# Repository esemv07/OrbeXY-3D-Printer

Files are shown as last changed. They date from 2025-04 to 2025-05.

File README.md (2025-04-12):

# OrbeXY 3D Printer  ⚙️🛠️

A fully DIY 3D printer that I designed

##  Overview

This is a small CoreXY 3D printer that I have designed from scratch including designing the Toolhead, Bed Assembly, Gantry and Belt System, as well as the Optical Endstops. See my journey of designing and building the printer [here](https://github.com/esemv07/OrbeXY-3D-Printer/blob/main/JOURNAL.md). This printer costs under $476.04AUD ($300USD). See my list of materials and prices [here](https://github.com/esemv07/OrbeXY-3D-Printer/blob/main/BOM.md).

## ✨ Key Features

- CoreXY Kinematics
- 100mm<sup>3</sup> Build Area
- Under 250mm<sup>3</sup> Full Size
- Runs Klipper
- Remote Printer
- Pico MMU Compatible
- NEMA 14 Stepper Motors used for the X and Y Axes
- NEMA 17 Stepper Motor with Lead Screw used for the Z Axis
- Optical Endstops for Homing

## 🏆 Goals

For this printer there were a few things that I wanted to achieve:
1. ***A Compact Overall Size:*** I wanted this printer to fit into small desk space so that people can have easy access to printing without having to have a big area dedicated to the printer. I wanted the build area to also be fairly small, at 100mm<sup>3</sup>, making the printer suitable for quick, and small prints. A lot of the choices I made while designing this printer centred around having a compact size while still preserving the full 100mm<sup>3</sup> build area.
2. ***Runs Klipper with Remote Printing:*** I wanted the printer to run Klipper to improve the overall easy and quality of the printer. On top of this I wanted to have remote printing, so that you can start prints from anywhere and come home to an already started, or even finished print. This meant I had to consider the hardware I was using and how I could configure these parts into the Klipper software. This includes the Optical Endstops, which I designed myself, which will be configured to the Klipper file.
3. ***Pico MMU Compatible:*** I also wanted this printer to be able to print multicoloured if desired. To achieve this I have made the printer compatible with the Pico MMU, meaning that multicoloured prints can be printed if desired. This also meant that in the Klipper configuration file, I had to configure the MMU to make sure that I could still use it via remote printing.
4. ***Separated Spool Holder:*** I decided that in this printer, I would have the spool holder separate from the main printer. This aligns with my goal for the size constraints meaning that if the user does not have enough desk space for the spool as well, the spool could be stowed underneath the desk even while printing. The spool holder is connected to the printer via bowden tubing that will run from the spool holder, into the extruder. The same will apply for if the Pico MMU is used. The spool holders can stay under the desk as well as the Pico MMU and the bowden tubing will run from the Pico MMU to the extruder.

## 📋 Checklist

### Design:
- [x] Toolhead
- [x] Bed Assembly
- [x] Z Axis System
- [x] X and Y Axis Belt System
- [x] Screen Holder
- [ ] Motherboard and Battery Mount
- [ ] Spool Holder
- [ ] Full CAD Model

Here is the [link](https://a360.co/3FXQvPA) to my live updating Full CAD Model!

### Firmware:
- [ ] Remote Printing
- [ ] Configured Optical Endstops
- [ ] Pico MMU Configured
- [ ] Full Klipper config File

### Build:
- [ ] Assemble Gantry
- [ ] X and Y Axis Belt System
- [ ] Z Axis Assembly
- [ ] Bed Assembly
- [ ] Screen and Electronics
- [ ] Full Build

### Tuning:
- [ ] To be added

## 📸 Photos

### Design:

Will add when it is finished

### Build:

Will add as I build it

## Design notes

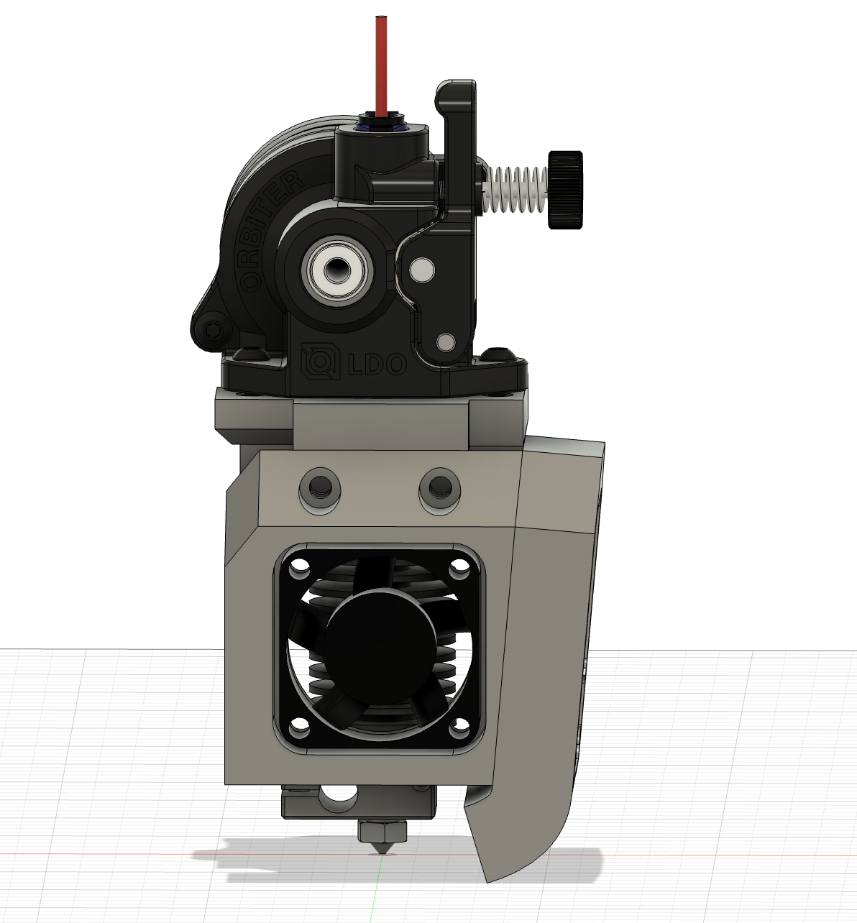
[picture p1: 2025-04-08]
progress-images/CAD-11:03:2025-1.png

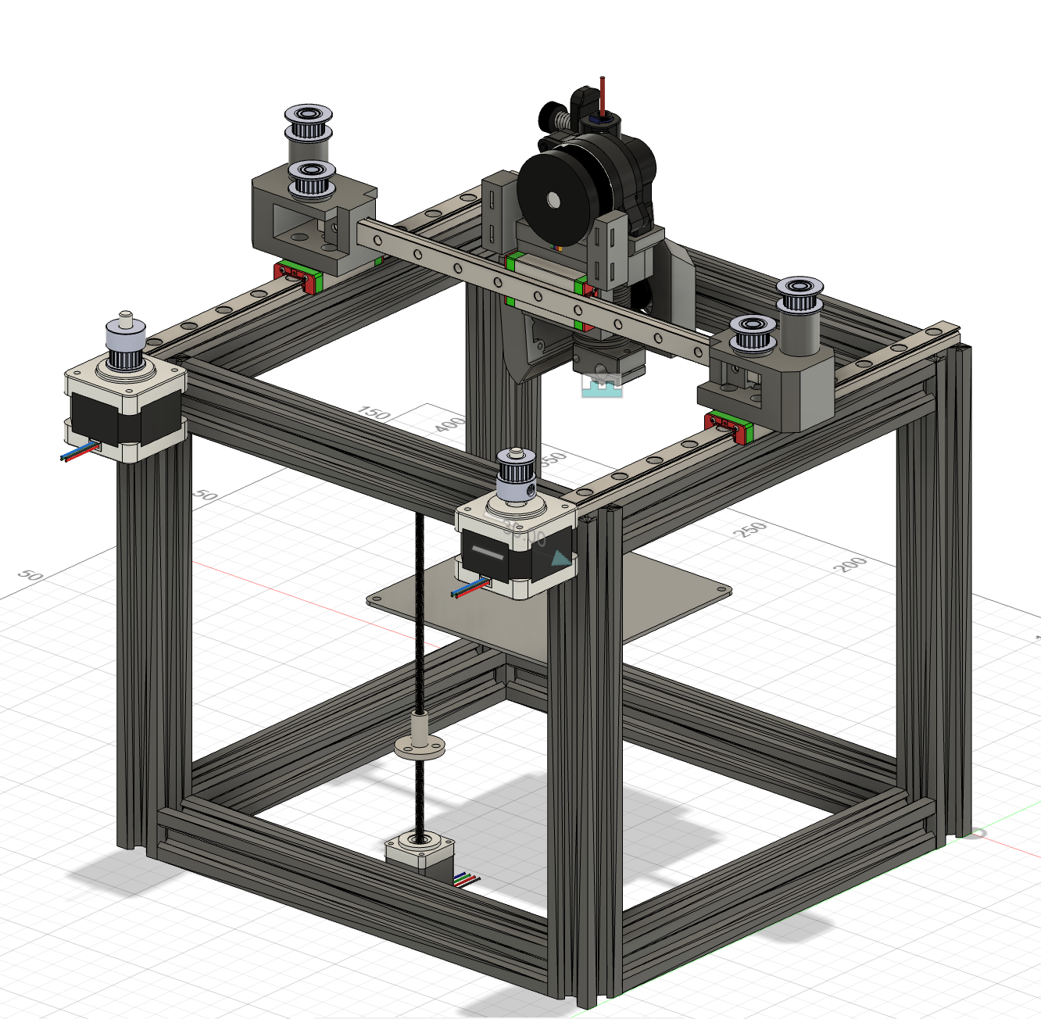
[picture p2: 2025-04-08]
progress-images/CAD-29:03:2025-2.png

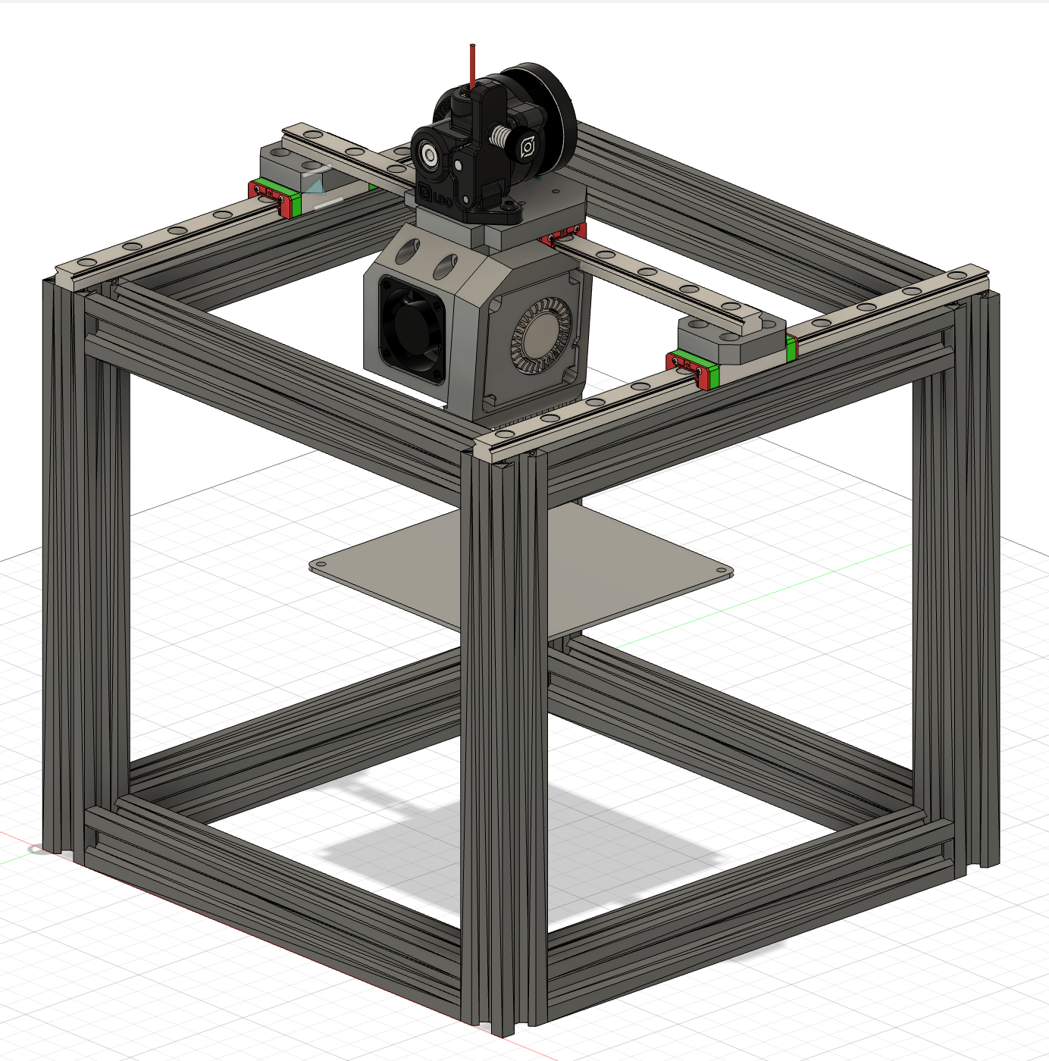
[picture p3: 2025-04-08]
progress-images/CAD-12:03:2025-1.png

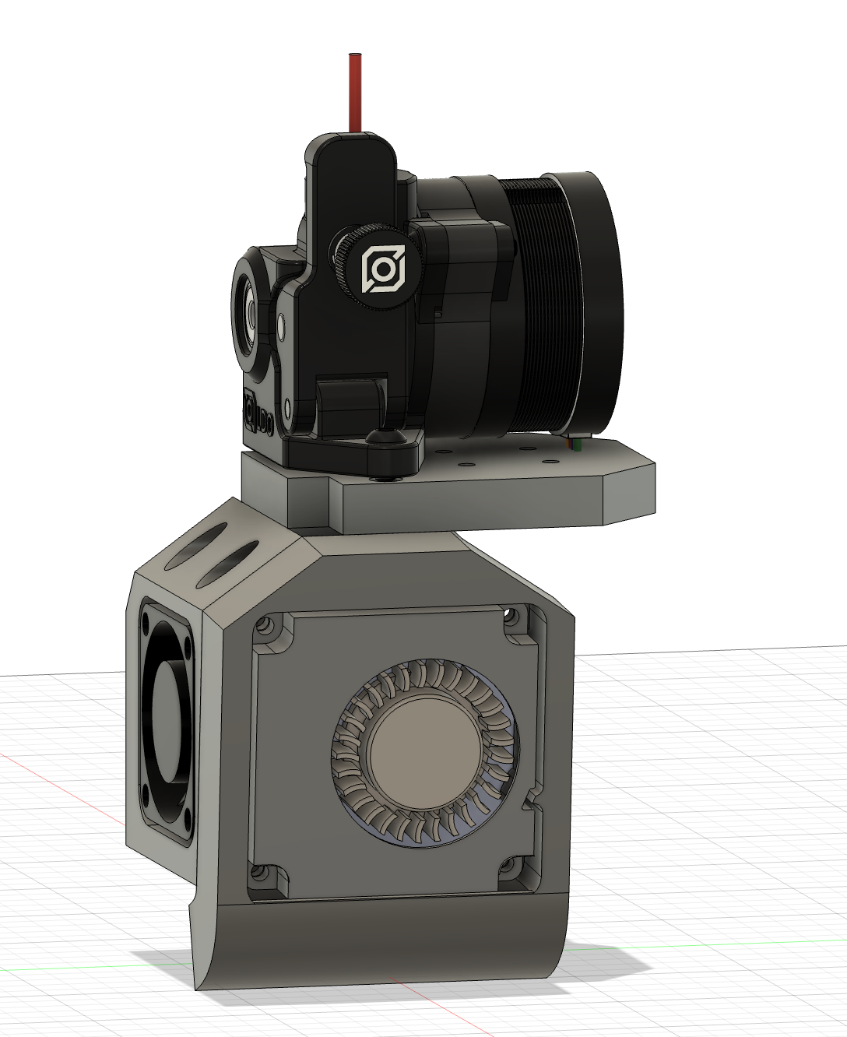
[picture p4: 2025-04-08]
progress-images/CAD-11:03:2025-2.png

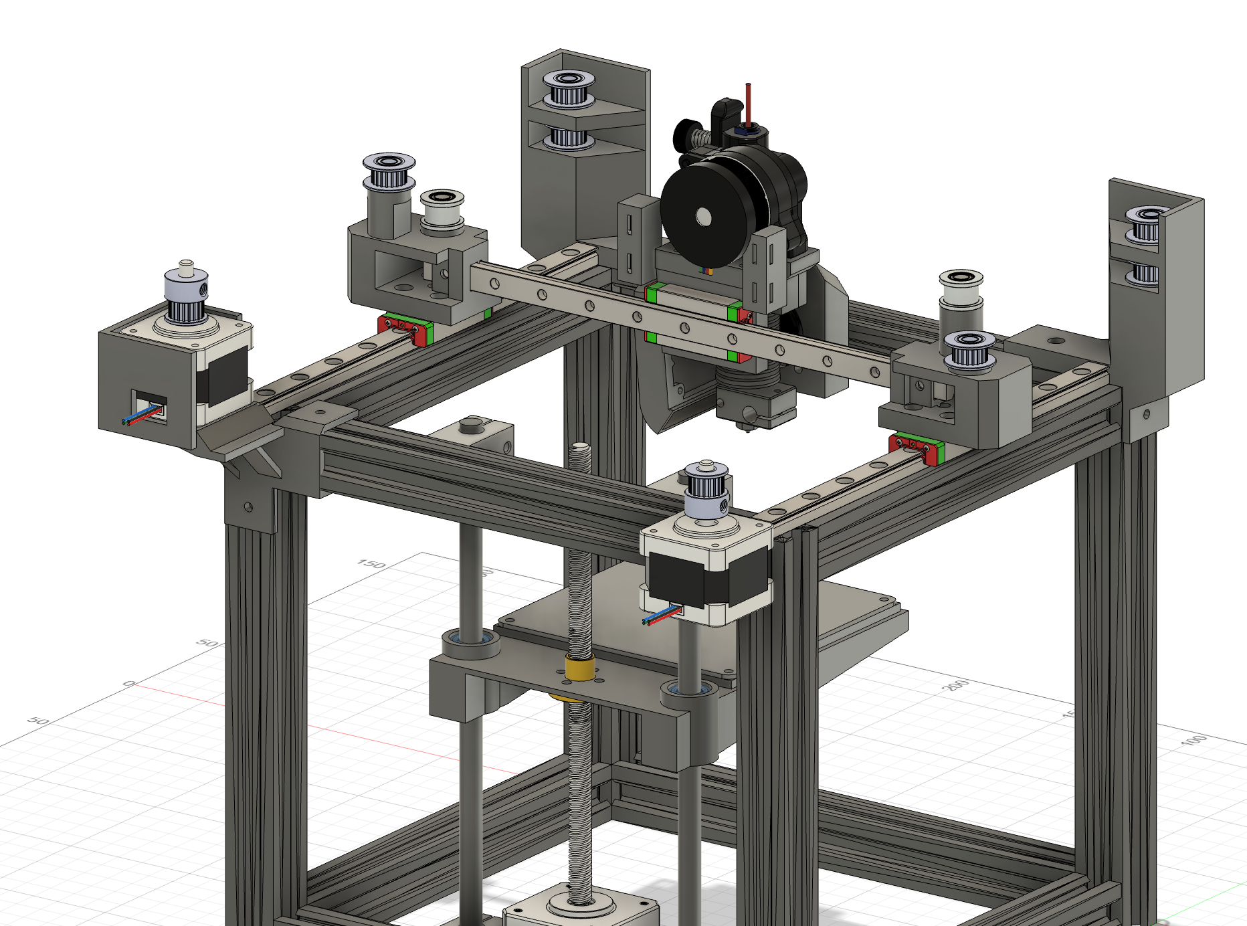
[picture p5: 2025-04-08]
progress-images/CAD-02:04:2025-2.png

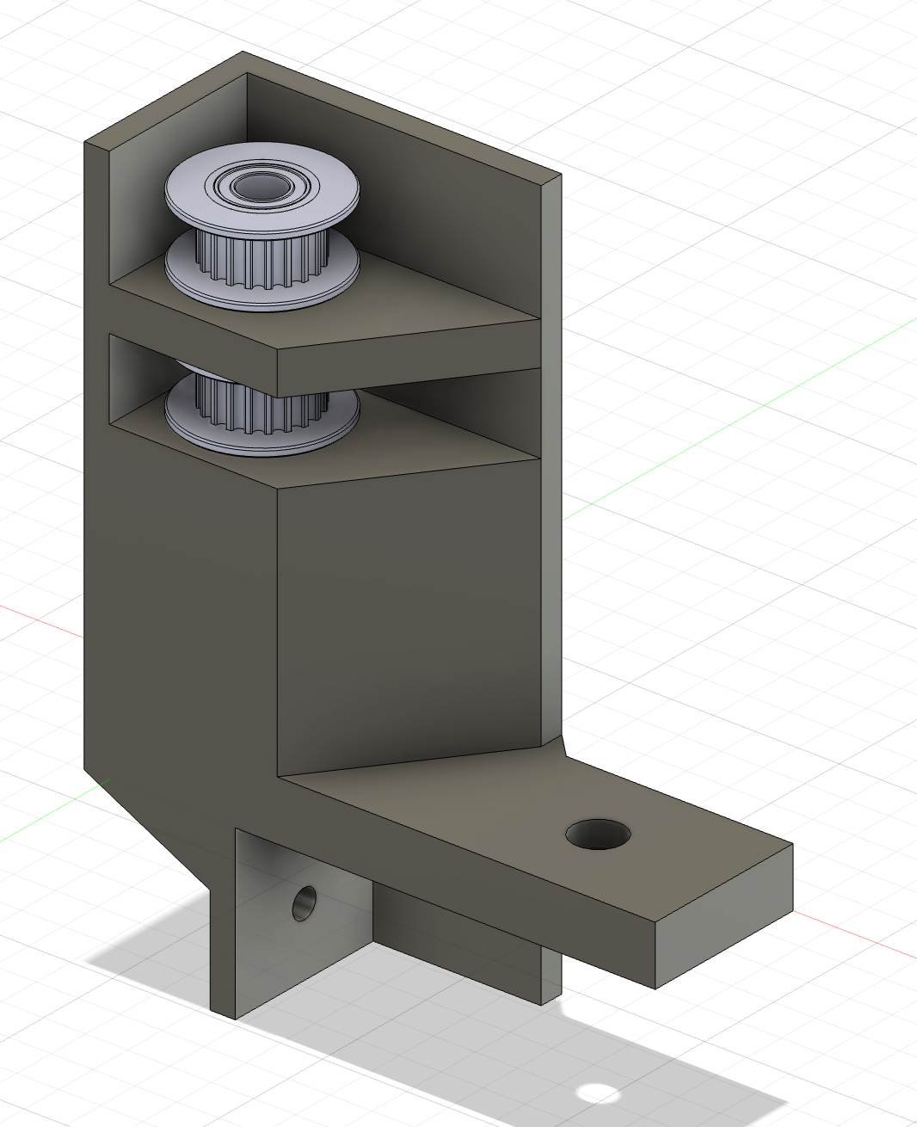
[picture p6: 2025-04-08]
progress-images/CAD-01:04:2025-1.png

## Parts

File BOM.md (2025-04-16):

# Bill Of Materials

Budget: $476.04AUD ($300USD)

> [!NOTE]  
> Prices may decrease as there is an upcoming sale.

> [!IMPORTANT]  
> Welcome deal will be used for the LCD Display Screen

| Category | Item | Price (AUD) | Quantity | Vendor | Link |
|---|---|---|---|---|---|
| Gantry ↓ | Aluminium Extrusions | $4.39 | 12 | AliExpress | [200mm 2020 T-slot Aluminum Profile](https://www.aliexpress.com/item/1005002845068178.html) |
| | MGN9H Linear Rails | $16.49 | 3 | AliExpress | [MGN9H Linear Rail](https://www.aliexpress.com/item/1005002937465647.html) |
| | GT2 Timing Pulley | $4.38 | 1 x 2pcs | AliExpress | [GT2 Timing Pulley](https://www.aliexpress.com/item/1005007708631215.html) |
| | GT2 20T Pulley | $2.46 | 6 | AliExpress | [GT2 20T 5mm Bore Pulley](https://www.aliexpress.com/item/1005005166638596.html) |
| | GT2 Smooth Idler Pulley | $2.46 | 2 | AliExpress | [GT2 Smooth 5mm Bore Pulley](https://www.aliexpress.com/item/1005005166638596.html) |
| | GT2 Timing Belt | $3.42 | 1 | AliExpress | [GT2 Closed Loop Timing Belt 6mm](https://www.aliexpress.com/item/32477498985.html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) |
| | NEMA 14 Stepper Motor | $8.35 | 2 | AliExpress | [NEMA 14 0.9 Degree 35MM Stepper Motor](https://www.aliexpress.com/item/1005008564455087.html) |
| Toolhead ↓ | Orbiter V2.0 | $36.59 | 1 | AliExpress | [Orbiter Extruder V2.0](https://www.aliexpress.com/item/1005006369780118.html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) |
| | E3D V6 Hotend | $7.71 | 1 | AliExpress | [E3D V6 Hotend 24V Short with PTFE](https://www.aliexpress.com/item/1005003651646732.html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) |
| | 3010 Axial Fan | $3.23 | 1 | AliExpress | [3010 Axial Fan 24V](https://www.aliexpress.com/item/1005003999728858.html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) |
| | 4010 Blower Fan | $3.68 | 1 | AliExpress | [4010 Blower Fan 24V](https://www.aliexpress.com/item/1005003999728858.html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) |
| | LDO Stepper Motor | $38.06 | 1 | AliExpress | [LDO-36STH20-1004AHG](https://www.aliexpress.com/item/1005005709255487.html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) |
| Bed Assembly ↓ | Mini Heated Bed | $17.44 | 1 | OpenBuilds | [Mini Heated Bed](https://us.openbuilds.com/mini-heated-bed/) |
| | Magnetic PEI Plate | $17.42 | 1 | AliExpress | [120x120mm Magnetic PEI Sheet](https://www.aliexpress.com/item/1005006868711474.html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) |
| | Silicone Foam Sheet | $1.53 | 1 | AliExpress | [100x100x3mm Red Silicone Foam Mat](https://www.aliexpress.com/item/1005008602779260.html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) |
| | NEMA 17 Motor w/ Lead Screw  | $26.79 | 1 | AliExpress | [NEMA17 Stepper Motor T8 Lead Screw Kit](https://www.aliexpress.com/item/1005004105159462.html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) |
| | Linear Rod | $4.13 | 2 | AliExpress | [200x8mm Stainless Steel Rod](https://www.aliexpress.com/item/1005008351656218.html) |
| | LM8UU Linear Bearing | $3.54 | 1 x 2pcs | AliExpress | [LM8UU Linear Bushing 8mm](https://www.aliexpress.com/item/1005008687738190.html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) |
| | SK8 Linear Rail Mount | $9.93 | 1 x 4pcs | AliExpress | [SK8 Linear Bearing Rail Shaft Support](https://www.aliexpress.com/item/4000909598267.html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) |
|  Electronics ↓ | SKR MINI E3 V3.0 Motherboard | $47.59 | 1 | AliExpress | [BIGTREETECH BTT SKR MINI E3 V3.0 Motherboard](https://www.aliexpress.com/item/1005008626893863.html) |
| | LCD Display Screen | $12.72 | 1 | AliExpress | [BIGTREETECH MINI 12864 V2.0 LCD Display Screen](https://www.aliexpress.com/item/1005006135086424.html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) |
| | Power Supply | $27.24 | 1 | eBay | [24V 350W Power Supply](https://www.ebay.com.au/itm/116529752336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) |
| | Plug and Switch Module | $3.61 | 1 | AliExpress | [Power Switch AC Power Outlet](https://www.aliexpress.com/item/32857063415.html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,scm-url:1007.40196.417130.0,pvid:38387bd7-0782-4954-80dd-48ccc1529973,tpp_buckets:668%232846%238110%231995&pdp_ext_f=%7B%22order%22%3A%22622%22%2C%22eval%22%3A%221%22%2C%22sceneId%22%3A%2230050%22%7D&pdp_npi=4%40dis%21AUD%213.80%211.68%21%21%212.24%210.99%21%402103146c17441867923614998e6107%2166407555495%21rec%21AU%21%21ABX&utparam-url=scene%3ApcDetailTopMoreOtherSeller%7Cquery_from%3A) |
| | Raspberry Pi Zero 2 W | N/A | 1 |(From Home) | N/A |

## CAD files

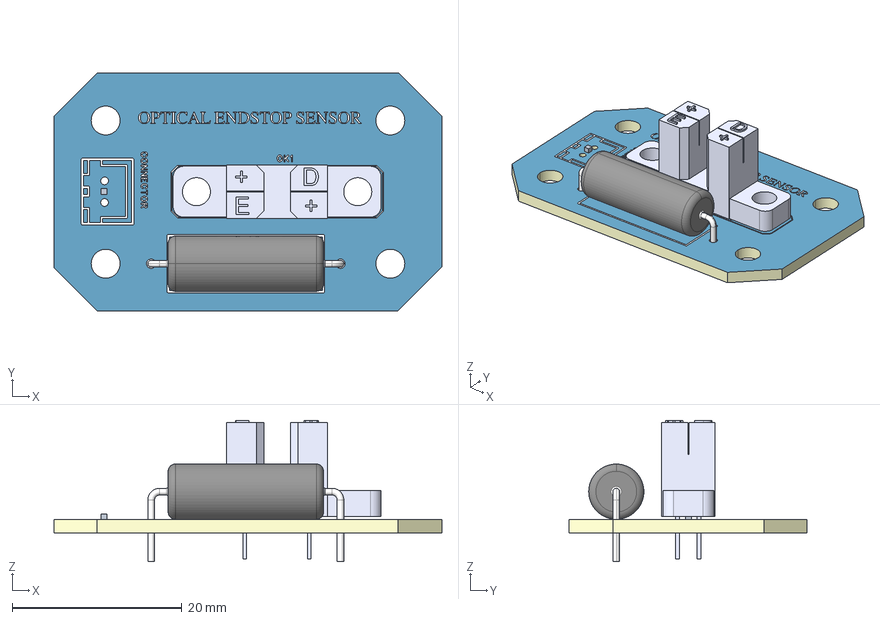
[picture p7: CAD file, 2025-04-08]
pcb/3D_1-PCB_PCB_Optical Endstops_2025-04-07.step
45.7 x 28.0 x 16.7 mm
Board~oxxd
TopCopper~oxxd
BottomCopper~oxxd
TopSilkscreen~oxxd
TopFpcStiffener~oxxd
BottomFpcStiffener~oxxd
TCST-2103~SENSORS-TH_TCST2103~oxxd
RES-TH_L18.3-W6.5-P22.30-D0.8~RES-TH_L18.3-W6.5-P22.30-D0.8~oxxd
JST_2-PIN_2.54MM~Connector_JST/JST - XH - Thru - 2Pin - 2.54mm~oxxd

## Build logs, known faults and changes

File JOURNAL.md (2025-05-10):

Made by: @esemv

Repository link: https://github.com/esemv07/OrbeXY-3D-Printer

Total hours so far: 64 hours

- [x] I have a 3D printer or will be getting one before March 21st

## What Makes My Printer Unique?
### Goals
- CoreXY Kinematics
- Under 280mm<sup>3</sup> total size
- 100mm<sup>3</sup> build volume
- Runs Klipper
- Pico MMU Compatible
- Remote Printing

### Achieved So Far
- [x] CoreXY Kinematics
- [x] Under 280mm<sup>3</sup> total size
- [x] 100mm<sup>3</sup> build volume
- [ ] Runs Klipper
- [ ] Pico MMU Compatible
- [ ] Remote Printing

## Day 1: March 8th 2025 
`Reseach` `PCB` `CAD`
- I reseached materials and what would be compatible with each other while staying in budget and my size constraints. I decided on an Extuder (Obbiter V2.0), and a Motherboard (BigTreeTech SKR Mini E3 V3.0). 

- I found a potential option for a printbed. It is quite difficult to find one that is in the correct size (100x100mm) as most come in 120x120 for the smallest size. I have decided that for the PEI Plate, I will buy a bigger size and cut it to the correct dimensions myself.

- I then designed a quick and simple PCB for the small Optical Endstop Sensors that I can use to keep the printhead in build area for all axes.

`Research: +3 hours` `PCB: +1 hour`

***+4 hours***

- I also researched different methods of multicolour printing and what would take up less space. Started designing a PCB for a Rotary Switcher Multi Material System, but then realised it would be to big for my printer size. I settled on using an MMU but I think I will design that last so I get the core mechanics good first.

CAD Mockup

- Started a rough CAD model in Fusion of the frame to visualise the dimensions. I may change the 2020 Aluminium Extrusions to 1010.

`Research: +1 hour` `CAD: +2 hours`

***+3 hours***

### Time Spent on This Day: 7 hours 
`Research: 4 hours` `PCB: 1 hour` `CAD: 2 hours`

<br><br>
## Day 2: March 9th 2025
`Research` `CAD`

CAD Frame Reshape

- I reshaped the frame so that there was more space on the inside and it will be less confusing for physical connection when I build it. It is now 200mm<sup>3</sup>, using 8 x _2020 160mm Aluminium Extrusions_ and 4 x _2020 200mm Aluminium Extrusions_.

- I then researched power supplies - how they work, how to know what voltage, current, and wattage to use. I also researched different methods for the Z-Axis on a CoreXY printer. I figured out that due to the very small scale of my printer I won't need to support all 4 corners of the build plate.

- I also reasearched hotends and how to connect them to my extruder which is direct drive. I am going to design a 3D printable mount so I can connect my direct drive extruder (Orbiter V2.0) with my hotend (Short E3D V6 Hotend with PTFE).

`Research: +3 hours` `CAD: +30 mins`

***+3 hours 30 mins***

### Time Spent on This Day: 3 hours 30 mins

`Research: 3 hours` `CAD: 30 mins`

<br><br>
## Day 3: March 10th 2025
`Research` `CAD`

- I researched toolhead designs and what fans I could use for mine and how I could mount the extruder to the hotend.

`Research: +1 hour`

***+1 hour***

CAD Toolhead

- I designed the toolhead with different parts that would mount together using screws and heatset inserts.

- There are 3 different parts: the part that mounts to the front of the hotend, the part that connects the axial fan to that part, and the part that mounts to the back of the hotend connecting the other fan and the extruder.

CAD Toolhead in Assembly

- Here is what it looks like in the full assembly so far.

`CAD: +3 hours`

***+3 hours***

CAD Toolhead Angled

- I also changed the angle of the side fan to blow the air more towards the nozzle and to optimise space on the toolhead.

`CAD: +1 hour`

***+1 hour***

### Time Spent on This Day: 5 hours

`Research: 1 hour` `CAD: 4 hours`

<br><br>
## Day 4: March 11th 2025

`Research` `CAD`

- I did more research on toolheads and realised that I need to add a channel for the air to flow towards the nozzle. I researched different methods of this for my design.

CAD Toolhead Airflow 1 CAD Toolhead Airflow 2

- I then applied this to my CAD model trying not to impede on the parts that I already had. This proved much harder than I expected and I had many iterations of it before I finally achieved a result that I wanted.

`Research: +30 mins` `CAD: +2 hours`

***+2 hours 30 mins***

### Time Spent on This Day: 2 hours 30 mins

`Research: 30 mins` `CAD: 2 hours`

<br><br>
## Day 5: March 12th 2025

`Research` `CAD`

- I researched the different axes motion systems and what motors and linear rails to use. I think I will use MGN7 rails and MGN7-H for the carriage and I will use NEMA 14 Stepper Motors. I still don't completely understand the belt system but I will model the rails and carriage connections first.

CAD Full Assembly

- I then added the linear rails to my full assembly and realised that it would be better to go with MGN9 rails and MGN9-H carriages so I added them instead. This meant I had to change the connection on the toolhead to fit on the MGN9-H carriage.

X-to-Y-Axis-Connector

- I also had to model some connectors to connect the X-Axis linear rail to the Y-Axis rails so that they could move together. Here is what they look like.

CAD Full Assembly

- I then put all the new and modified components together in the full assembly. Here's what it looks like to far!

`Research: +3 hours` `CAD: +3 hours`

***+6 hours***

### Time Spent on This Day: 6 hours

`Research: 3 hours` `CAD: 3 hours`

<br><br>
## Day 6: March 13th 2025

`Research` `CAD`

- I did a lot of research on the X-Axis and Y-Axis motion systems and how to implement them, it was quite confusing how both the belts connect to the toolhead as I originally thought that one would connect to the toolhead, and one to the ends of the linear rail. I understand it now though after quite a bit of research.

`Research: +1 hour`

CAD Full Assembly

- I got started on the CAD for these motion systems, so far I added the NEMA 14 stepper motors and GT2 20 Teeth Pulleys. Here is what it looks like in the full assembly so far.

`CAD: +1 hour`

***+2 hours***

### Time Spent on This Day: 2 hours

`Research: 1 hour` `CAD: 1 hour`

<br><br>
## Day 7: March 24th 2025

`Research` `CAD`

- I researched how to add the pulleys and belts to my system and espeecially how to connect them on the toolhead end.

- I realised that it might be better to have the X-Axis linear rail with the carraige facing forwards rather than upwards. This would mean that I had to redesign my X-to-Y-Connectors for the linear rails.

X-to-Y-Axis-Connector

- It was difficult to design these without heavily limiting the range of motion of the carraige in the X-Axis so I had _many_ iterations. Here is what the final design looks like. It screws onto the Y-Axis linear rail and the X-Axis rail slots into it and is secured with a srew.

`Research: +30 mins` `CAD: +2 hours`

***+2 hours 30 mins***

Toolhead Connector

- I then also had to edit the toolhead so that it would work with this new sideways rail system. Heres what it turned out like.

CAD Full Assembly

- This is what it would look like in the full assembly. I haven't adjusted any dimensions of anything else so it doesn't fit together properly yet.

`CAD: +1 hour 30 mins`

***+1 hour 30 mins***

### Time Spent on This Day: 4 hours

`Research: 30 mins` `CAD: 3 hours 30 mins`

<br><br>
## Day 8: March 28th 2025

`CAD`

- I realised that for the X-to-Y-Connector I need a different slot for the left side and the right side so that the linear rail can go all the way through.

CAD Full Assembly

- I then had to adjust the dimensions of the aluminium extrusions in order to fit the new connectors and adjust the positions of all the other components for the full assembly. Here is what it looks like.

`CAD: +3 hours`

***+3 hours***

### Time Spent on This Day: 3 hours

`CAD: 3 hours`

<br><br>
## Day 9: March 29th 2025

`Research` `CAD`

Pulley Mounts Belt Slots

- I added mounts at the corresponding heights to the X-to-Y-Connectors for the pulleys to sit for the belts. Here's what it originally looked like. I also added slots on the back of the Toolhead for the belts to feed through and here's what that looked like.

- I didn't like how bulky the X-to-Y-Connectors turned out so I did some research on how other people cut down on the size while still maintaining the function.

`CAD: +1 hour` `Research: +1 hour`

***+2 hours***

CAD Full Assembly

- I came up with this design to cut down on the size while still maintaining the same function as the other design. Here's what it looks like in the full assembly.

`CAD: +2 hours`

- I still need to add a mount the the _NEMA 14 Stepper Motors_ so that they are in the correct spots as well as adding pulleys on the front side of the printer for the belt. I think I will come back to this later.

***+2 hours***

### Time Spent on This Day: 4 hours

`Research: 1 hour` `CAD: 3 hours`

<br><br>
## Day 10: March 30th 2025

`Research` `CAD`

- I did some research on all the parts of the printbed. I had already chosen the heatbed and to have a magnetic PEI Plate. I decided on putting a _3mm Silicone Sheet_ under the heatbed as an insulator to separate the heat from the 3D printed base. I am using a _NEMA 17 Stepper Motor with Intergrated Lead Screw_ as well as 2 _8mm Linear Rods_ for support to control the Z-Axis movement of the bed.

Bed Assembly Bed Assembly 

- I designed the printbed around these things and here's what the finished bed assembly looks like by itself and with the motor, lead screw, and rods.

`Research: +1 hour` `CAD: +2 hours`

***+3 hours***

CAD Full Assembly

- Here is what the full assembly looks like so far. I think all I have left to do is to finish it is the X and Y Axis pulley and belt system and to add the endstops that I made at the start. Although I'll probably think of something else left to do later :pensive:.

### Time Spent on This Day: 3 hours

`Research: 1 hour` `CAD: 2 hours`

<br><br>
## Day 11: April 1st 2025

`CAD` `BOM`

- I worked on making the end pulley holders for the XY-Belt system. The reason they stick out on the side is because I have to leave enough inside space for the toolhead to reach every corner of 100mm<sup>2</sup>.

- I am going to secure the pulleys with a long screw going from the top into a heatset insert at the bottom. They are going to be separated by a platform.

- `CAD: +1 hour`

End Pulley Holder CAD Full Assembly CAD Full Assembly

- Here is what they look like by themselves and in the full assembly.

- I then worked on adding all the parts I have so far into my Bill Of Materials with links to where I will source them from and prices.

`BOM: +1 hours`

***+2 hours***

### Time Spent on This Day: 2 hours

`CAD: 1 hour` `BOM: 1 hours`

<br><br>
## Day 12: April 2nd 2025

`CAD`

- I created a holder/mount for the motor that sits on the right side of the frame (when looking from the front).

Motor Holder CAD Full Assembly

- I tried to add support to it from the diagonal to make sure that it would be strong enough to hold the weight of the motor. Here is what it looks like by itself and in the full assembly.

`CAD: +2 hours`

***+2 hours***

### Time Spent on This Day: 2 hours

`CAD: 2 hours`

<br><br>
## Day 13: April 5th 2025

`CAD`

- I first modelled the mount for the screen that I am using, the _BIGTREETECH MINI 12864 V2.0 LCD Display Screen_. This was difficult, as I had to figure out what to do to secure it.

- I also modelled corner brackets to connect the Aluminium Extrusions together.

- I changed the height of the of the pulleys so that they are both at the lowest possible height. This does a few things:
  1. Cuts down on filament used
  2. Puts less stress on the motor holder as it will have a centre of gravity closer to the bracket
  3. Makes the overall design smaller to fit into the size constraints that I have (250mm<sup>3</sup>)

- My Fusion finally decides to allow me to change the appearances of objects and components so I changed the colours of everything to what they will finally be.

First Render

- Here is what my first render looks like... I'm so excited it looks so cool and it's all coming together :grin:

`CAD: +4 hours`

***+4 hours***

### Time Spent on This Day: 4 hours

`CAD: 4 hours`

<br><br>
## Day 14: April 6th 2025

`CAD`

- I remodelled the motor mount and the end pulley holders so that they will fit into the the design for the corner mounts. They now correspond to the corner mounts to make it easier and more consistent.

Second Render

- Here is another render (yay!)

`CAD: +3 hours`

***+3 hours***

### Time Spent on This Day: 3 hours

`CAD: 3 hours`

<br><br>
## Day 15: April 9th 2025

`Research` `CAD`

- I modelled the second motor mount and also mounted the Z-Axis Endstop.

- I mounted the Z-Axis Endstop to the bottom of the top frame at the back. This is so that when the bed rises to the Layer 0 height, it will stop just before hitting the nozzle. I experimented with having the Endstop mounted to Bed Assembly itself but due to size constraints, realised that this wouldn't work.

Z-Axis Endstop CAD Full Assembly

- Here's what that looks like as well as the full assembly.

`CAD: +3 hours`

***+3 hours***

- I also did some research on Power Supplies. I calculated the full power draw and have settled on a _24V 350W Power Supply_. I will also use a _Plug and Switch Module_ so that I can plug in the wire that will connect to the wall and have the safety of being able to turn it on and off from the printer.

`Research: +2 hours`

***+2 hours***

- What I now have left to do is mounting the Power Supply and Plug and Switch Module to the printer as well as the Mainboard. I also need to mount a Raspberry Pi, so that I can run Klipper and have remote printing.

- I'm so close!!!

### :grin: :grin:

### Time Spent on This Day: 5 hours

`Research: 2 hours` `CAD: 3 hours`

<br><br>
## Day 16: April 10th 2025

`BOM`

- I updated my Bill of Materials with any relevant parts that I had not yet added. I realised for a few of the parts I had linked that they were 'Max. 1 pcs/shopper' but I needed multiple of the part, so I had to find new sellers that allowed me to get more than 1.

- I realised this is a much bigger problem than I thought, and I need to update more parts than I anticipated. I'll fix it later though.

`BOM: +1 hour`

***+ 1 hour***

- Also, Fusion stopped opening my files on my laptop so I'll have to fix that :confounded:

### Time Spent on This Day: 1 hour

`BOM: 1 hour`

<br><br>
## Day 17: April 15th 2025

`Orders` `BOM`

- I ordered my first part from AliExpress which is the [LCD Screen](https://www.aliexpress.com/item/1005006135086424.html). This is the item I decided to use the Welcome Deal for so I got it for $10.55AUD.

`Orders: +1 hour`

- I then went through the Bill of Materials some more to make sure all the parts I had there well within price range, and had reasonable shipping times and fees.

`BOM: +2 hours`

***+ 3 hours***

### Time Spent on This Day: 3 hours

`Orders: 1 hour` `BOM: 2 hours`

<br><br>
## Day 18: April 17th 2025

`Orders`

- I ordered another 15 parts which was almost all of the other parts I need. They are set to be delivered somewhere between the 20th and 30th of April.

- I wasn't able to order the Hotend because for some reason the payment kept failing; I think AliExpress had flagged the card as suspicious for no reason. I tried to submit an appeal for the payment but it wouldn't allow me to. So I tried to chat with customer support but I was stuck going round in circles with the bad AI 'customer support worker' that kept suggesting the same solutions that had already not worked :roll_eyes:

- I also ordered my Power Supply from a local eBay seller which was cheaper and easier.

`Orders: +3 hours`

- I also realised after ordering one of the parts, that the seller was very suspicious so the order may not get fulfilled. Hopefully I can get a refund.

- So now I guess it's just a case of waiting :hourglass_flowing_sand:	:alarm_clock:

***+ 3 hours***

### Time Spent on This Day: 3 hours

`Orders: 3 hours`

<br><br>
## Day 19: April 18th 2025

`Orders`

- I continued to try to pay for the Hotend; I tried many different sellers but all of them failed. Eventually I ended up having to use a different card to pay for it and it worked first time.

- No idea why it was so difficult but it was pretty annoying. At least I got it ordered in the end. :neutral_face:

`Orders: +1 hour`

***+ 1 hour***

### Time Spent on This Day: 1 hour

`Orders: 1 hour`

<br><br>
## Day 20: April 23th 2025

`Orders` `Assembly`

- My first item arrived today :partying_face: which was the LCD Screen

- I put the mount for it on to print, so that when the other parts arrive, I can mount it to the Aluminium Extrusions

`Assembly: +30 mins`

***+ 30 mins***

### Time Spent on This Day: 30 mins

`Assembly: 30 mins`

<br><br>
## Day 21: April 25th 2025

`Orders` `Assembly`

- A bunch of parts arrived today! :tada::tada: Here is what arrived:
    - GT2 Timing Pulleys
    - Orbiter v2.0 Extruder
    - 3010 Axial Fan
    - 4010 Blower Fan
    - Power Switch and Socket*
    - GT2 Timing Belt
    - PC3 M6 Connector
    - M3 Heatset Inserts
    - Magnetic PEI Plate
    - GT2 20 Tooth Pulley
    - GT2 No Tooth Pulley
    - Silicone Foam Mat
    - M3 Bolt and Nut Set
    - 2020 200mm Aluminium Extrusions
    - MGN9H Linear Rails
 
    - Power Supply (from eBay)

 - *When I ordered the Power Switch and Socket, I accidentally ordered it without the wires. It's actually cheaper and easier for me to just buy it again but with the wires rather than buying the wires and crimping tools, so that's I'll do.

 - The Power Supply is larger than I expected so I will have to redesign the holder/mount for it.

 - I set the Corner Brackets to print so that I can assemble the Aluminium Extrusions.

`Assembly: +30 mins`

***+ 30 mins***

### Time Spent on This Day: 30 mins

`Assembly: 30 mins`

<br><br>
